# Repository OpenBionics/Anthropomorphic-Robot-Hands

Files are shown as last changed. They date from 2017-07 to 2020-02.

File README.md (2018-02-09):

# OpenBionics - Anthropomorphic Robot Hands

Anthropomorphic, adaptive robot hand with tendon-driven, multidirectional fingers. The fingers employ an actuation mechanism that can achieve both flexion/extension and adduction/abduction concurrently in the metacarpophalangeal (MCP) joint, using two actuators. The two actuators offer increased power transmission during the execution of precise grasping and dexterous, in-hand manipulation tasks. A design optimization framework utilizes results of hand anthropometry studies to derive key parameters of the actuation design.

## Contents

In this repository you can find:
* CAD files of a bidirectional finger 
* ROS package software for dual actuators operation
* Design optimization framework 
* Archive of prototype images
* CAD files of the anthropomorphic robot hand will be uploaded soon

## Notes

Please open a [GitHub issue](https://github.com/OpenBionics/Anthropomorphic-Robot-Hands/issues) if you encounter any problem.

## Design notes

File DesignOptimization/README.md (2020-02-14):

## Introduction

A design optimization framework to derive optimal differential mechanism parameters, according to abduction motion of metacarpophalangeal (MCP) joint. For the index adduction/abduction, we employ the selectively lockable differential mechanism that has the ability to vary its displacement when fingers are locked. To simplify the kinematic analysis, we assume that tendons remain vertical and the input force of the differential mechanism is equally distributed to the remaining 3 digits.

## Working Example

In Figure 1, the design optimization parameters of the differential mechanism are presented.

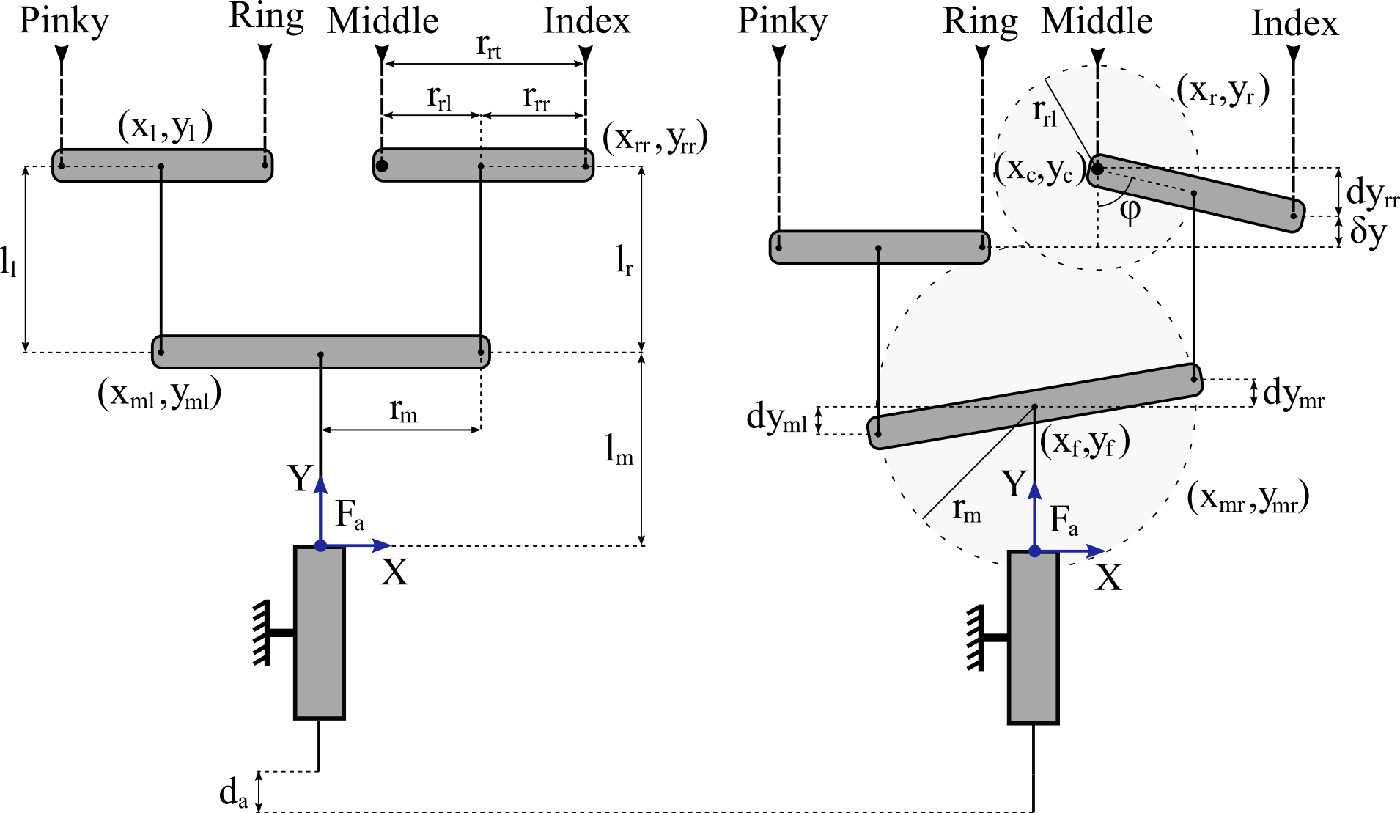
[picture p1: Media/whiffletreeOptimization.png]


Figure 1. Design optimization parameters.

Given the actuator displacement d<sub>a</sub>, the main bar radius r<sub>m</sub>, the index bar radius r<sub>rl</sub>, the length of tendon tendon from actuator to the main bar l<sub>m</sub>, and the length of tendon tendon from the main bar to the index bar l<sub>r</sub>, we obtain the configuration of the index bar (x<sub>r</sub>,y<sub>r</sub>) and of the main bar (x<sub>mr</sub>,y<sub>mr</sub>) by solving a nonlinear equality constraint optimization scheme. Next, we can derive the full configuration of the differential mechanism. 

## Notes

Please open a [GitHub issue](https://github.com/OpenBionics/Anthropomorphic-Robot-Hands/issues) if you encounter any problem.

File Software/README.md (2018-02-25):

## Introduction

The OpenBionics hand_controller ROS package. With this package you 2 [Dynamixel RX-28](http://support.robotis.com/en/product/actuator/dynamixel/rx_series/rx-28.htm) servo motors can be controlled concurrenlty in ROS, along with an [external power supply](http://www.trossenrobotics.com/p/power-supply-12vdc-5a.aspx), a [power supply adapter](http://www.robotis.us/smps2dynamixel/), and a [USB2Dynamixel adapter](http://support.robotis.com/en/product/auxdevice/interface/usb2dxl_manual.htm). Note that there are various ways to implement the control of the 2 Dynamixel, but our suggestion is similar with our tested experimental procedure.

## Installation
This package has been developed and tested in ROS Indigo on Ubuntu 14.04.5 LTS. After ROS installation, create a workspace.

```
$ mkdir -p ~/hand_ws/src
$ cd ~/hand_ws/src
$ catkin_init_workspace
```

Next, clone the hand_controller package and the dependencies in the src directory.
```
$ cd ~/hand_ws/src 
$ git clone https://github.com/OpenBionics/Anthropomorphic-Robot-Hands.git
$ git clone https://github.com/vanadiumlabs/arbotix_ros.git
$ git clone https://github.com/arebgun/dynamixel_motor
```

Then, compile the code and source the workspace.
```
$ cd ~/hand_ws/ 
$ catkin_make
$ . devel/setup.bash
```

Make all the files executable.
```
$ cd ~/hand_ws/src/hand_controller/src/ 
$ chmod +x hand_controller_flex.py && chmod +x hand_controller_adduction.py && chmod +x double_motor_publisher.py && chmod +x double_motor_publisher_sequence.py
```

## Working Example
Connect the servo motors, the USB2Dynamixel, and the power supply as shown [here](http://support.robotis.com/en/product/auxdevice/interface/usb2dxl_manual.htm). Then, check that the USB2Dynamixel adapter is properly connected.
```
$ ls /dev/ttyUSB*
```
If you get ```/dev/ttyUSB0``` continue the procudre, if not check the list bellow.
* If you get  ```/dev/ttyUSB1```, unplug all your USB devices and plug only the USB2Dynamixel adapter. An alternative solution is to navigate to the main controller launch file and change the port name.
```
$ cd ~/hand_ws/src/hand_controller/hand_controller/launch
$ gedit controller_hand_manager.launch
```
Then source the workspace again.
```
$ . devel/setup.bash
```
* If you get permission denied error, change the permissions of the user from the home directory.
```
$ sudo chmod 777 /dev/ttyUSB0
```

In a new terminal run a roscore.
```
$ roscore
```
Set the servo motors IDs through the arbotix_terminal application. 
```
$ arbotix_terminal /dev/ttyUSB0 57142 # The baud rate of Dynamixel AX-12  is 1000000
```
From the arbotix_terminal application list the motors.
```
>> ls
```
To rearrange the IDs, connect only the first servo motor and move its ID.
```
>> mv 1 2
```
Then connect both servo motors and list them.
```
>> ls
```
You should get.
```
   1    2 .... .... .... .... .... .... ....
.... .... .... .... .... .... .... .... ....
```
Exit the arbotix_terminal application (Ctrl-C) and the roscore. Start the controller manager.
```
$ roslaunch hand_controller controller_hand_manager.launch
```
Then, start the controllers for each servo motor.
```
$ roslaunch hand_controller start_flex_controller.launch
$ roslaunch hand_controller start_adduction_controller.launch
```

Next, get feedback from the flexion and the abduction servo motor.
```
$ rosrun hand_controller hand_controller_flex.py
$ rosrun hand_controller hand_controller_adduction.py
```

To control the servo motors.
```
$ rosrun hand_controller double_motor_publisher.py 1.5 1.0 
```
The last numbers represent the servo motor positions for the flexion and the abduction respectively. Note that the desired servo motor positions are absolute and in radians. Since the servo motors can rotate from 0-300<sup>o</sup>, the equivalent radian angles are 0-5.235 rad. In our working example the flexion motor desired position is 57.3<sup>o</sup> and the abduction motor desired position is 85.9<sup>o</sup>.

In case you want to control the motors sequenceally.
```
$ rosrun hand_controller double_motor_publisher_sequence.py
```
You can watch the manipulation of a cylindrical object with this sequence [here](https://youtu.be/w6tnvIsw6BY).

## Notes
Please open a [GitHub issue](https://github.com/OpenBionics/Anthropomorphic-Robot-Hands/issues) if you encounter any problem.

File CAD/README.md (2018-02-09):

## Introduction

The CAD files of a bidirectional finger equipped with a tendon-driven actuation mechanism. The metacarpophalangeal (MCP) joint can implement both flexion/extension and adduction/abduction concurrently, using 2 actuators.

## Contents

In this folder you can find:
* CAD files of a bidirectional finger test bed (SLDPRT) 
* CAD files for 3D printing (STL)
* CAD files of Dynamixel AX-12 as found [here](https://grabcad.com/library/dynamixel-ax-12a-1)

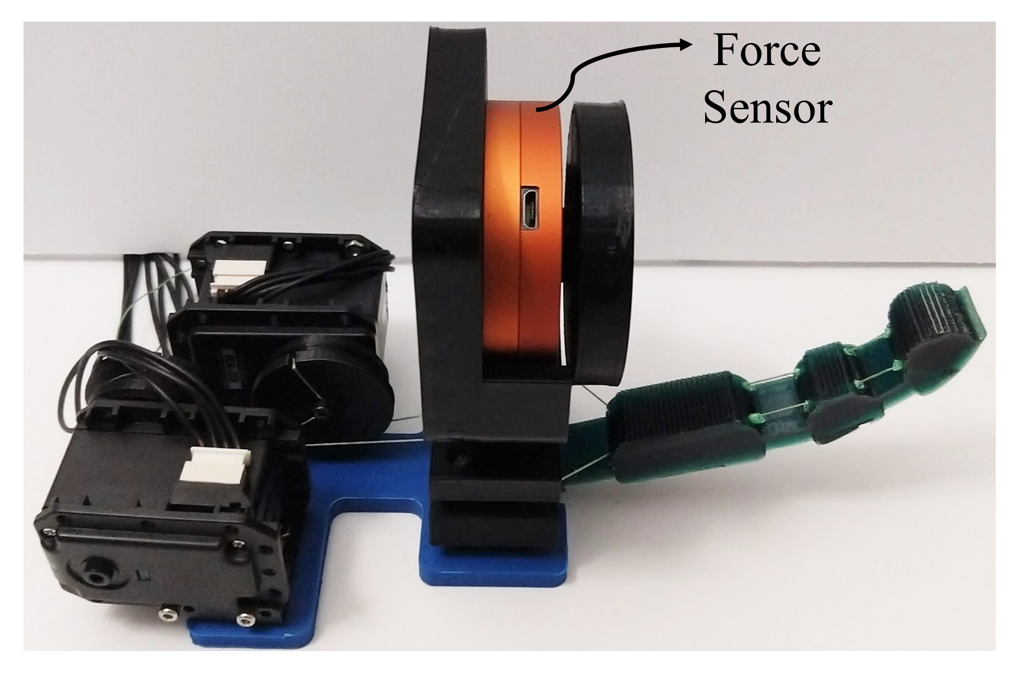
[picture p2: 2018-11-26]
Media/forceSensor.png

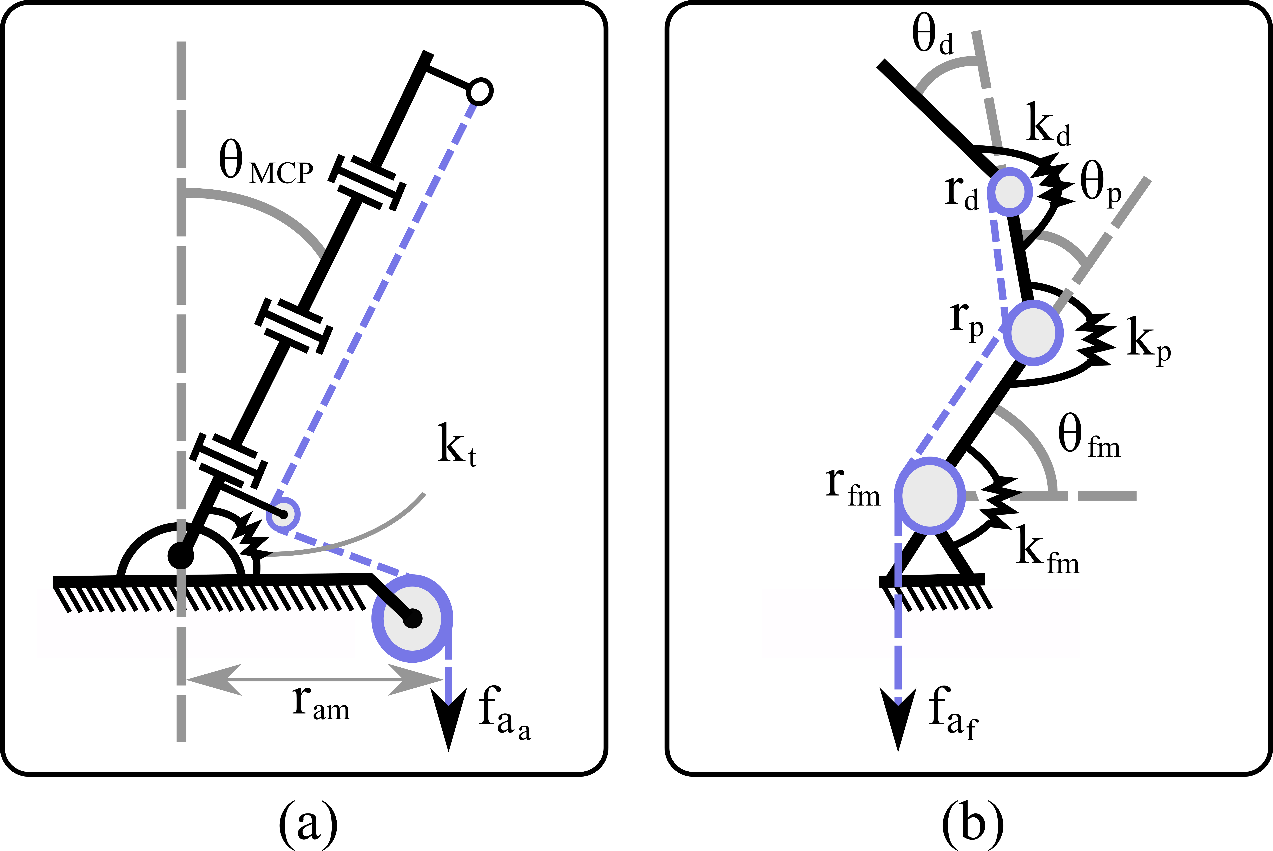
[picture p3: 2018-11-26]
Media/fingerModelAnalysis_col.png

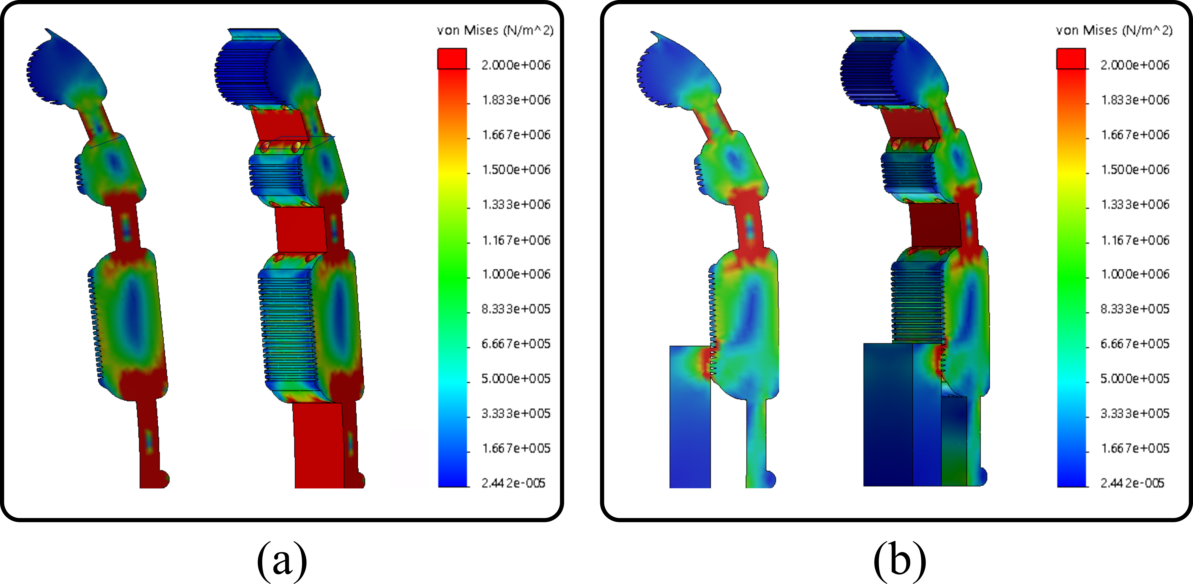
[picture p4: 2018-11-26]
Media/fingerStressAnalysis.png

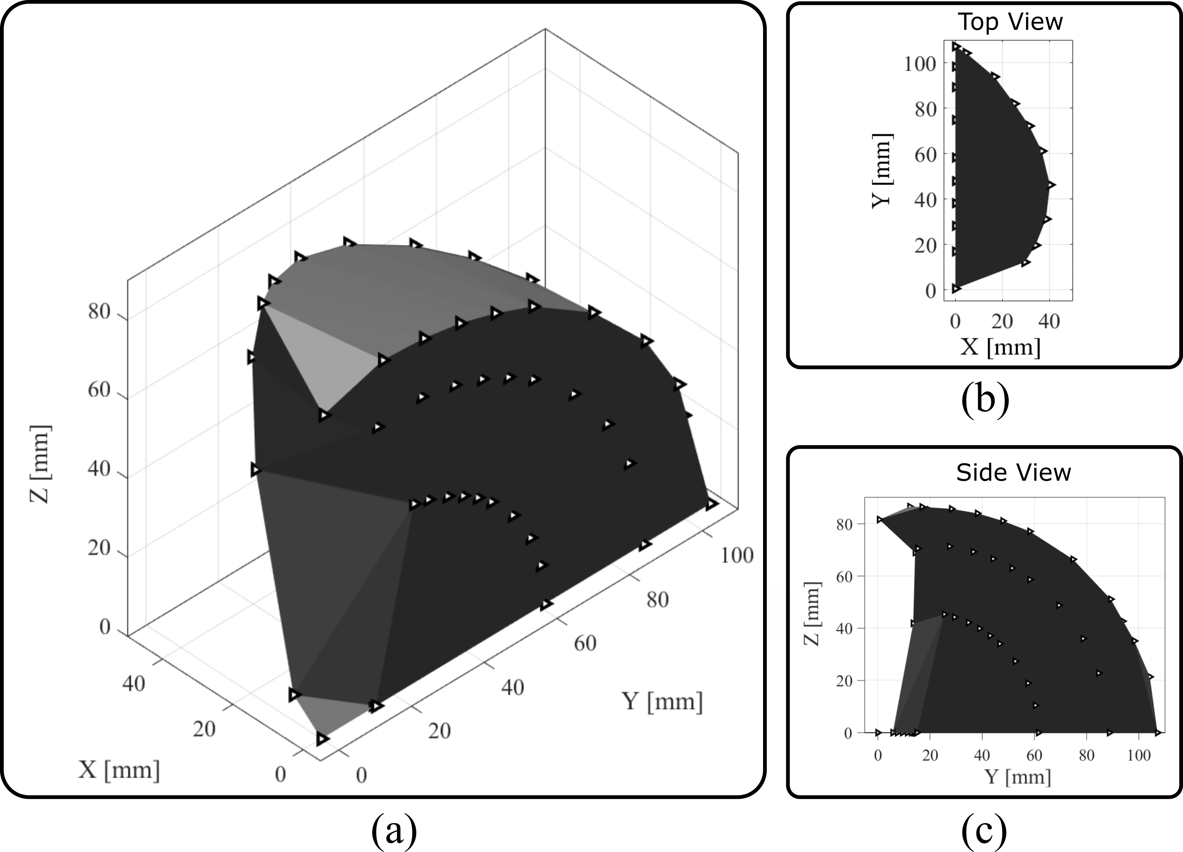
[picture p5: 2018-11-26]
Media/Workspace.png

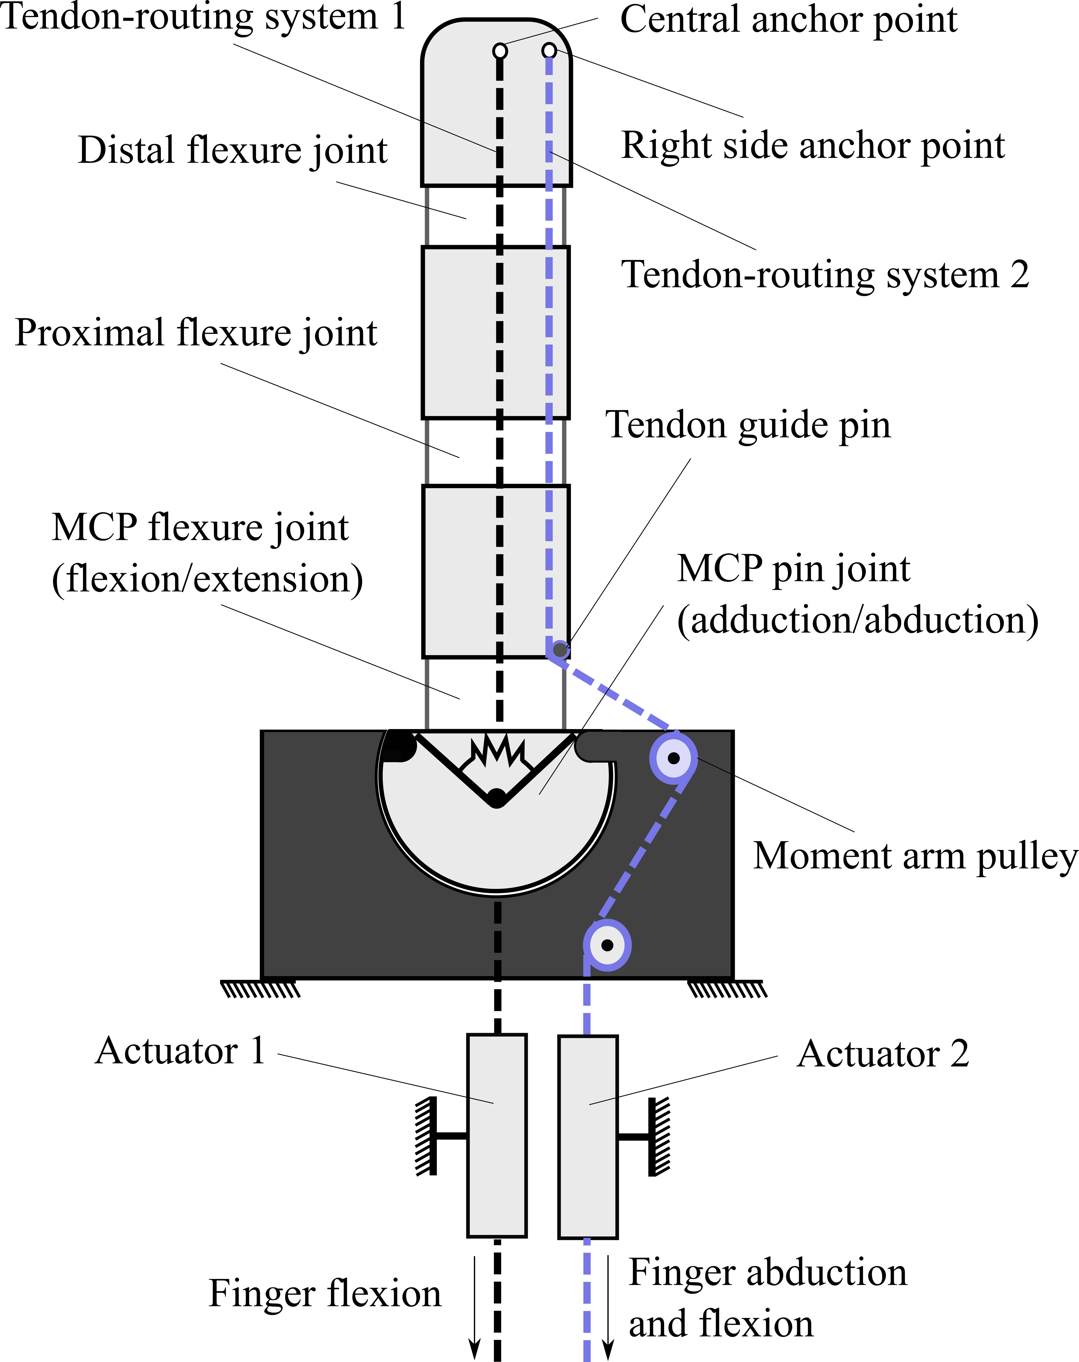
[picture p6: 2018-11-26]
Media/fingerSketch2_1_col.png

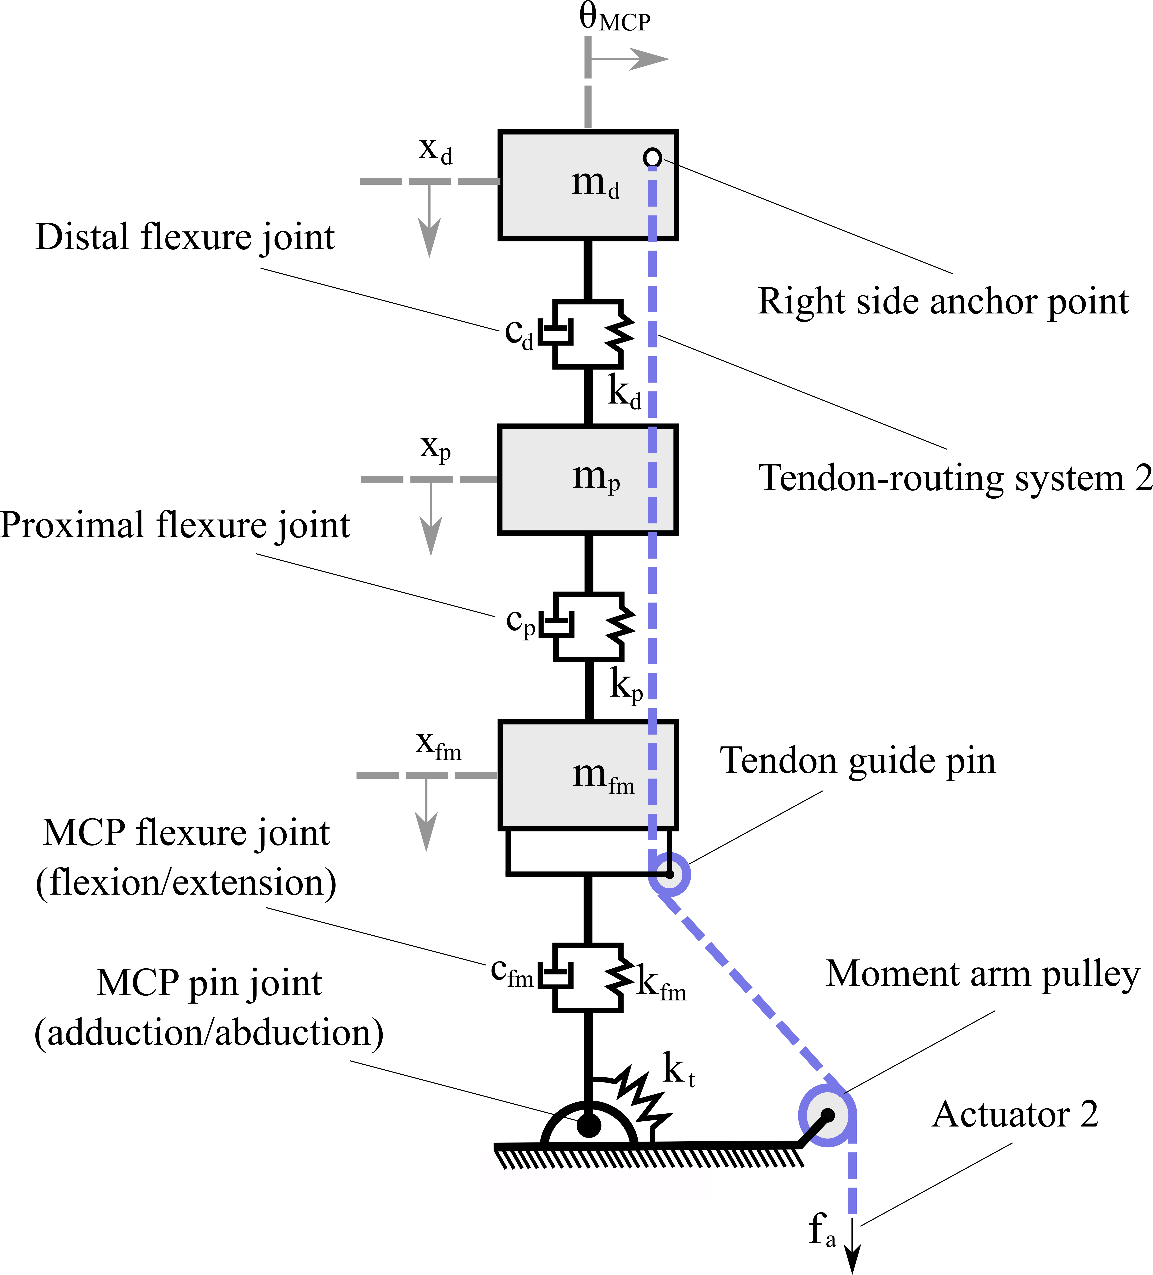
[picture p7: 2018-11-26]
Media/fingerModel_col.png

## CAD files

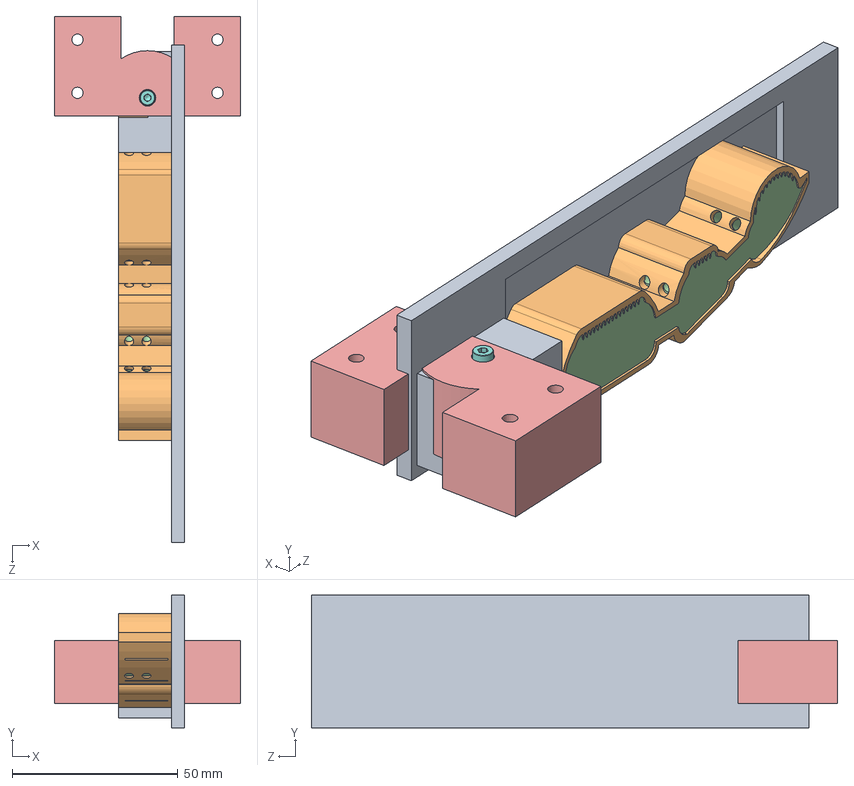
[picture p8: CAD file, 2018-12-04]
CAD/FingersHDM/src/index/indexMoldAssembly.SLDASM
56.2 x 40.0 x 158.5 mm
rotatingFingerLink
indexHDM
base
coilSpring
hex thin nut chamfered gradeab_iso
socket head cap screw_iso

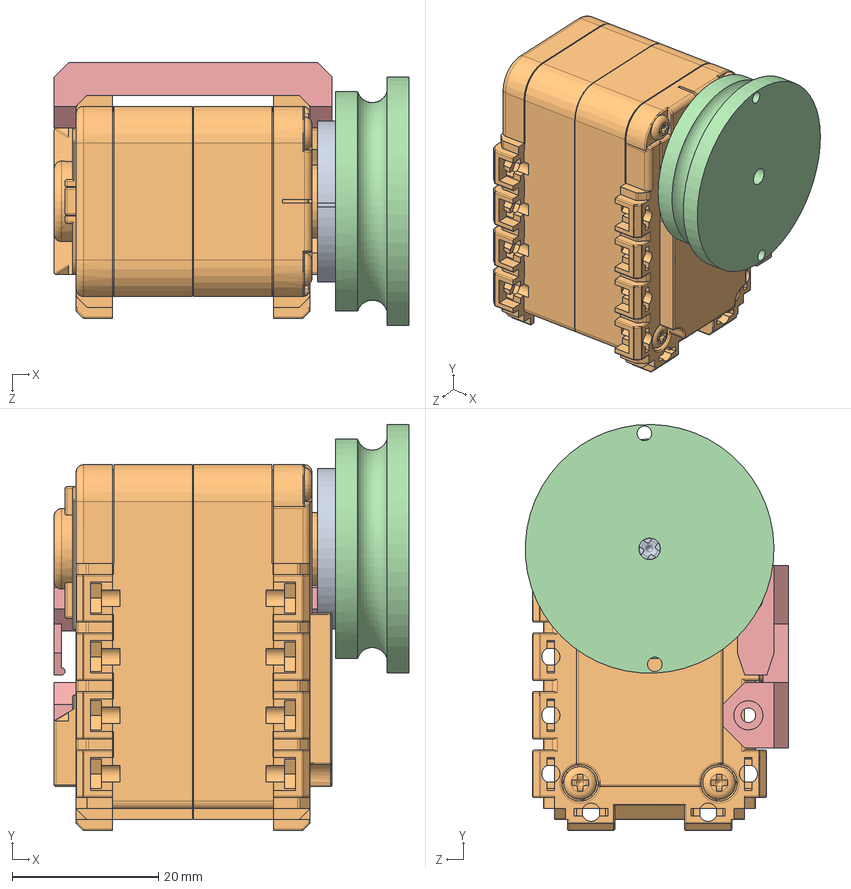
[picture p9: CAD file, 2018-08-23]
CAD/Servo/AX12_Base.SLDASM
48.5 x 55.5 x 36.0 mm
ax12_wheel
ax12_box
ax12_cog
servoPulleyRX28
AX12Base

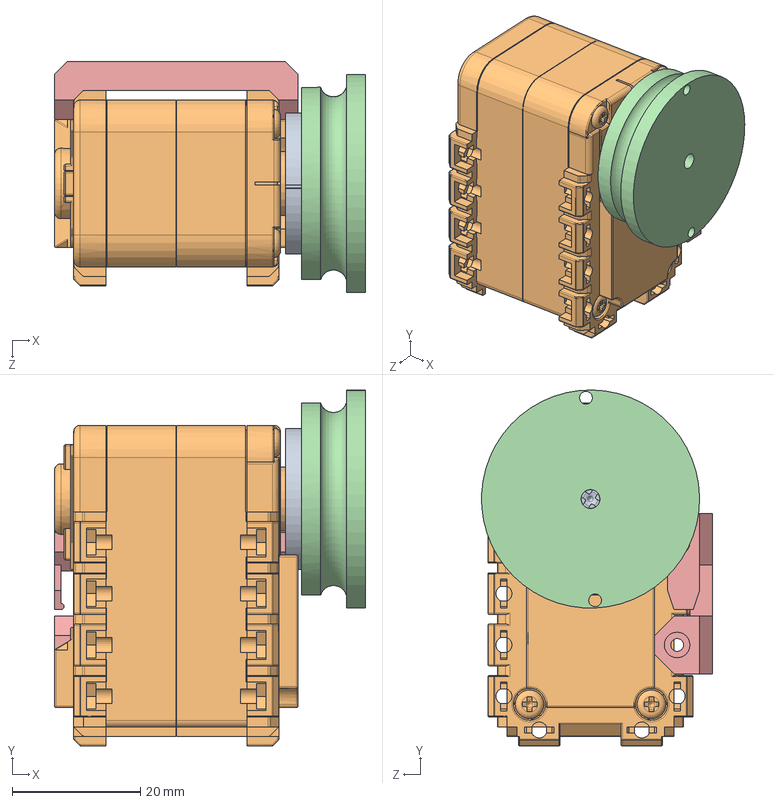
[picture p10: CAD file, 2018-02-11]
CAD/Servo/AX12_BaseR.SLDASM
48.5 x 55.5 x 36.0 mm
ax12_wheel
ax12_box
ax12_cog
servoPulleyRX28
AX12Base

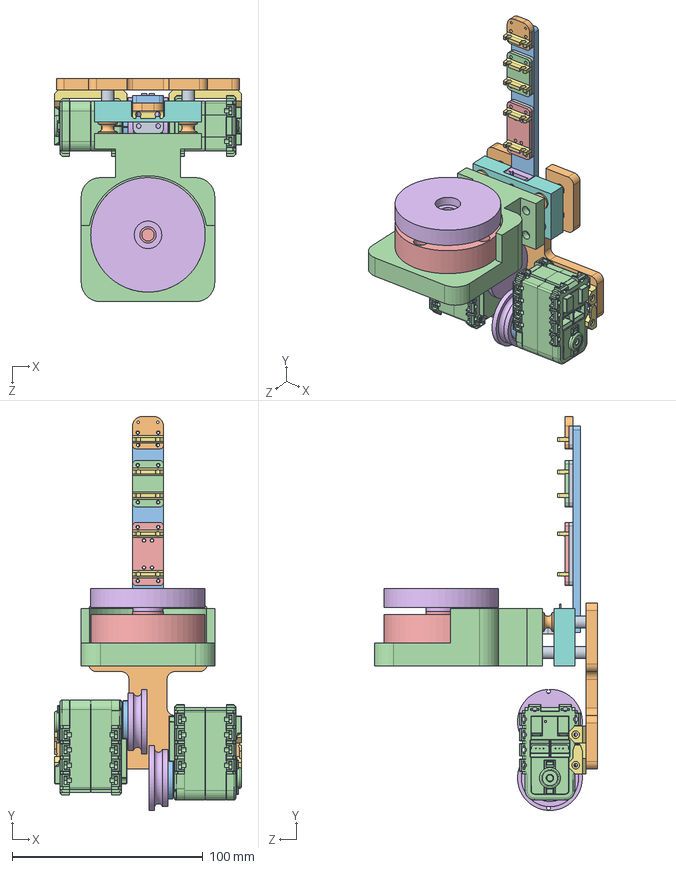
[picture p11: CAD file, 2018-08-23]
CAD/BidirectionalFinger/BidirectionalFinger.SLDASM
98.0 x 206.4 x 117.0 mm
middleJointBase
middleDIP
middleElastomer
middleMIP
middlePIP
rotatingFingerBase
tubeDriver x 5
palmUpBase
thumbMechanismDriver
base
ax12_wheel x 2
ax12_box x 2
ax12_cog x 2
servoPulleyRX28 x 2
AX12Base x 2
hexalobular socket pan head_iso x 5
spacer x 6
spacePulley x 2
coilSpring
forceSensorBase
VarienseFS101
forceSurface

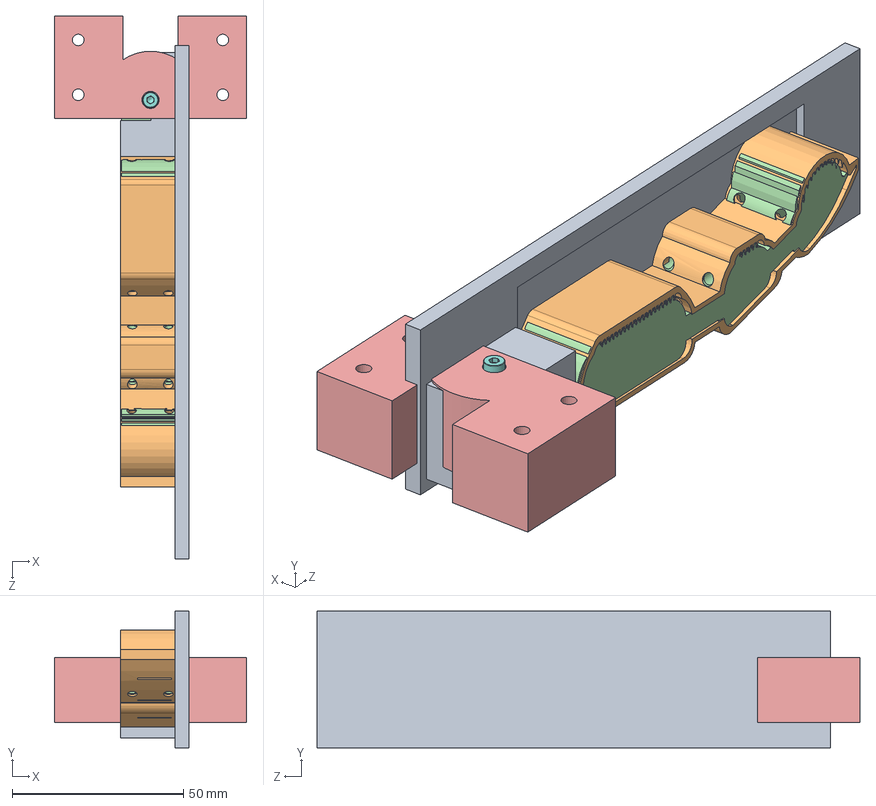
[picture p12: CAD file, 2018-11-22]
CAD/FingersHDM/src/thumb/fingerMoldAssembly.SLDASM
56.2 x 40.0 x 158.5 mm
rotatingFingerLink
fingerHDM
base
coilSpring
hex thin nut chamfered gradeab_iso
socket head cap screw_iso

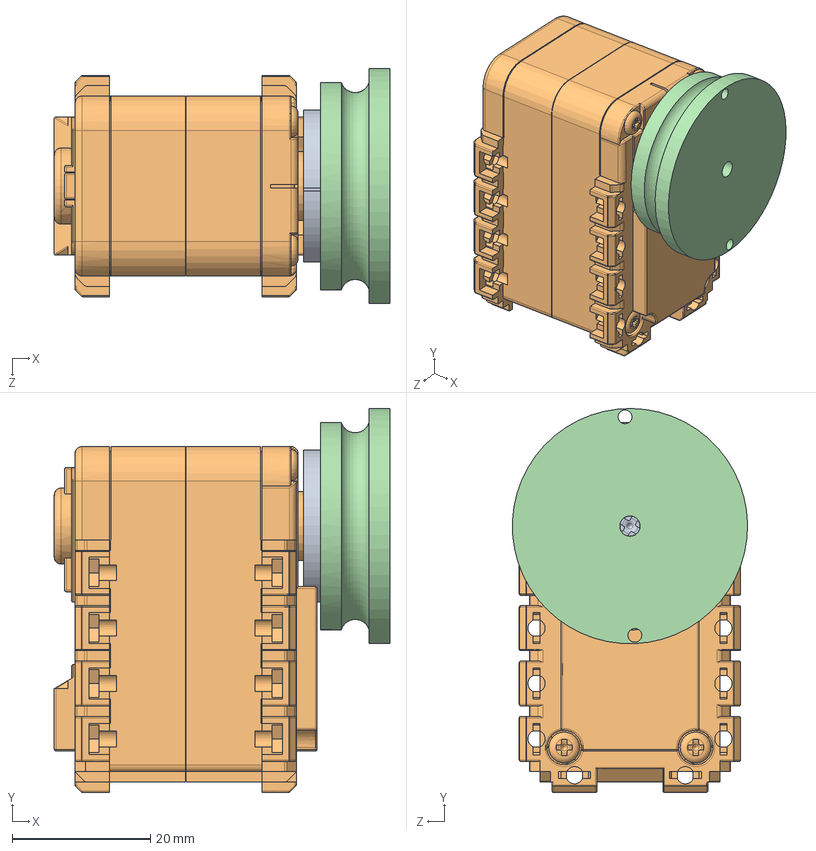
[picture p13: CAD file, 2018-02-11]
CAD/Servo/AX12.SLDASM
48.5 x 55.5 x 34.0 mm
ax12_wheel
ax12_box
ax12_cog
servoPulleyRX28

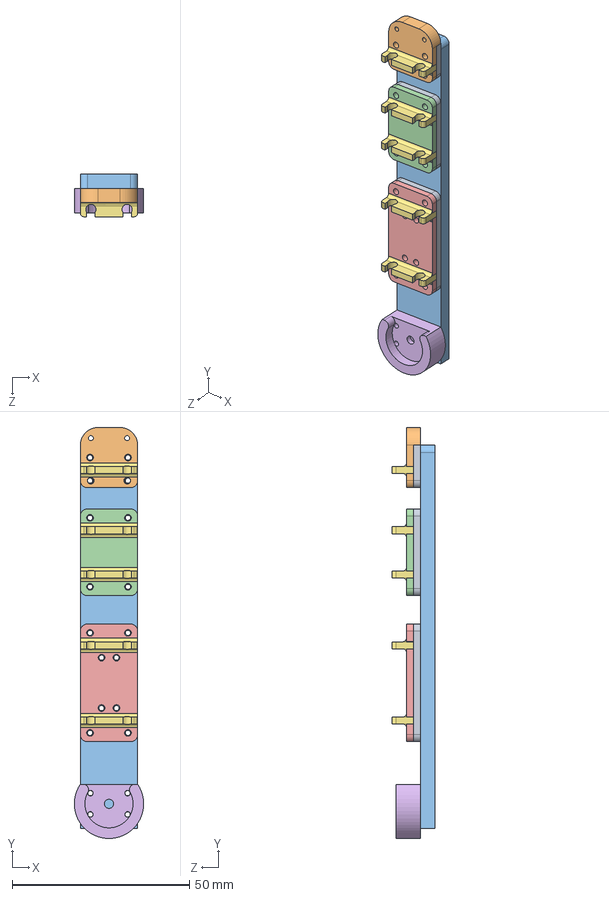
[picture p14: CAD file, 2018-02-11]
CAD/BidirectionalFinger/Middle.SLDASM
19.6 x 115.9 x 12.0 mm
middleJointBase
middleDIP
middleElastomer
middleMIP
middlePIP
rotatingFingerBase
tubeDriver x 5

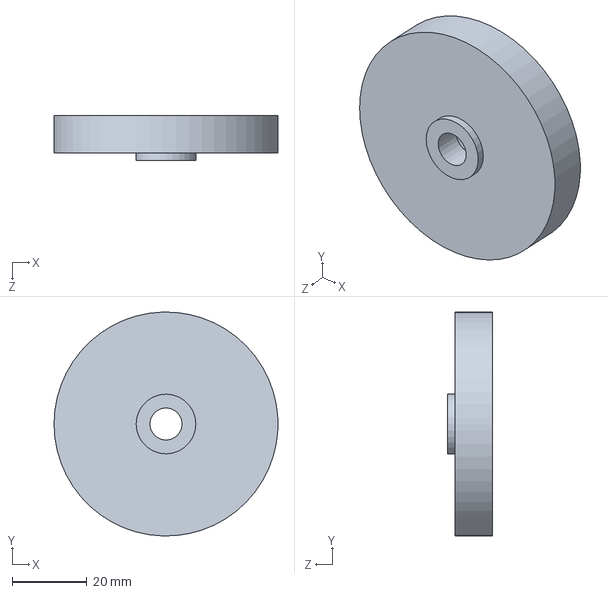
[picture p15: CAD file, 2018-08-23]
CAD/BidirectionalFinger/forceSurface.SLDPRT
60.0 x 60.0 x 12.0 mm

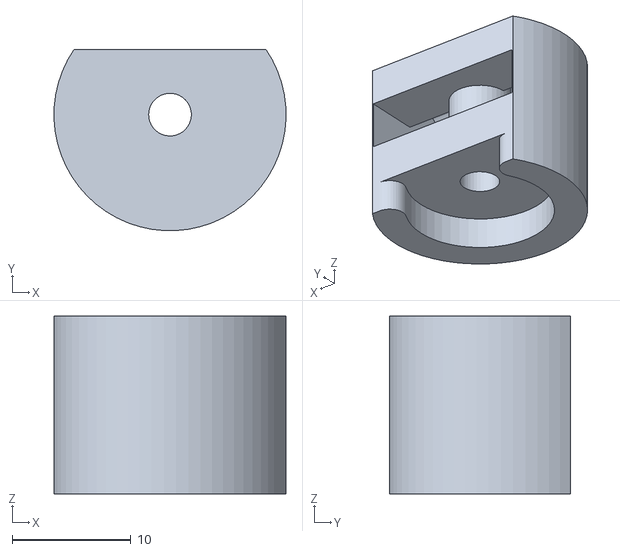
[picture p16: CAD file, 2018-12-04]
CAD/FingersHDM/commonParts/rotatingFingerLink.STL
19.6 x 15.3 x 15.0

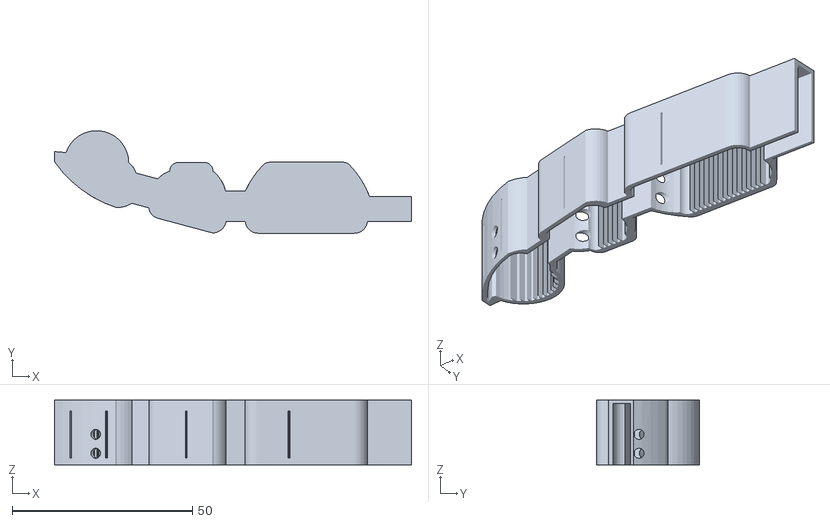
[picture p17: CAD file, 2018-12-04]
CAD/FingersHDM/index/indexMold.STL
98.9 x 28.4 x 18.0

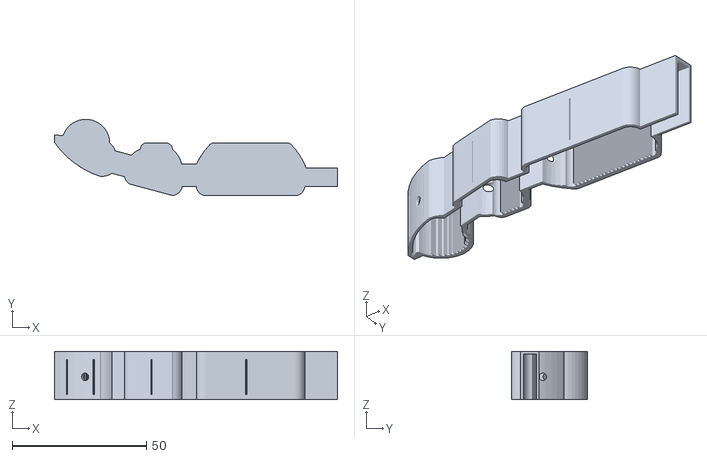
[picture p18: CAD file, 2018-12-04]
CAD/FingersHDM/middle/middleMold.STL
105.4 x 28.4 x 18.0

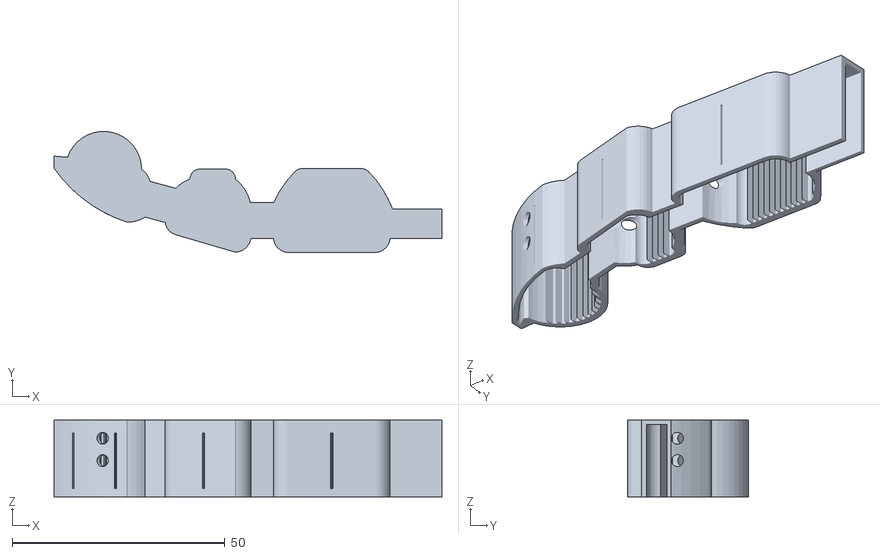
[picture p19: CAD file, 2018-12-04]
CAD/FingersHDM/pinky/pinkyMold.STL
91.1 x 28.4 x 18.0

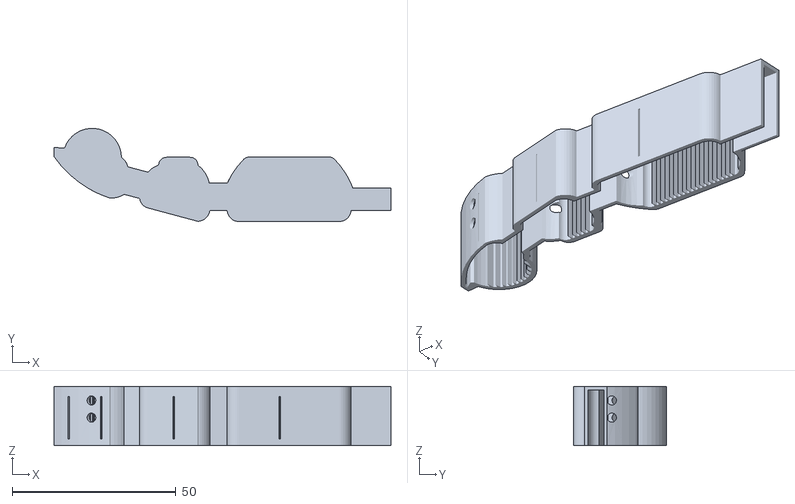
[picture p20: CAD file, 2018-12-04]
CAD/FingersHDM/ring/ringMold.STL
102.8 x 28.4 x 18.0

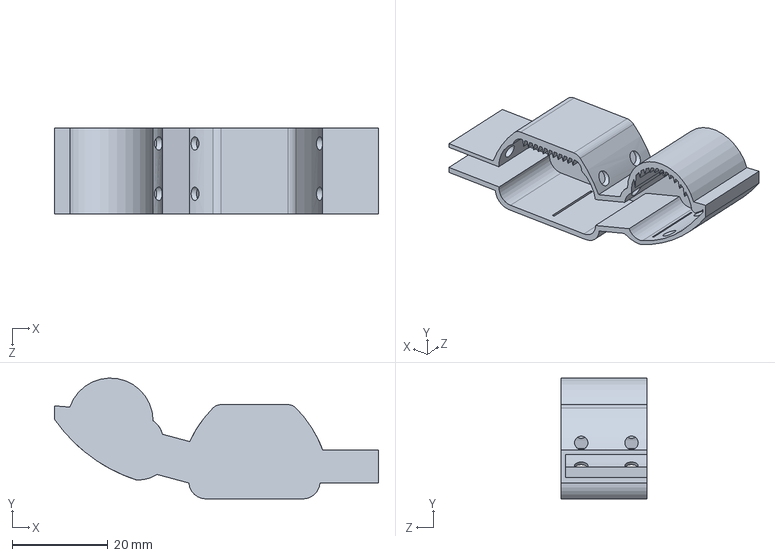
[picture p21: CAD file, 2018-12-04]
CAD/FingersHDM/src/thumb/thumbMold.SLDPRT
67.6 x 25.2 x 18.0 mm

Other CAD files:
CAD/FingersHDM/src/commonParts/rotatingFingerLink.SLDPRT
CAD/FingersHDM/src/middle/middleMold.SLDPRT
CAD/FingersHDM/src/pinky/pinkyMold.SLDPRT
CAD/FingersHDM/src/ring/ringMold.SLDPRT
CAD/BidirectionalFinger/CylindricalObject.SLDPRT
CAD/BidirectionalFinger/VarienseFS101.SLDPRT
CAD/BidirectionalFinger/base.SLDPRT
CAD/BidirectionalFinger/coilSpring.SLDPRT
CAD/BidirectionalFinger/forceSensorBase.SLDPRT
CAD/BidirectionalFinger/middleDIP.SLDPRT
CAD/BidirectionalFinger/middleElastomer.SLDPRT
CAD/BidirectionalFinger/middleJointBase.SLDPRT
CAD/BidirectionalFinger/middleMIP.SLDPRT
CAD/BidirectionalFinger/middlePIP.SLDPRT
CAD/BidirectionalFinger/palmUpBase.SLDPRT
CAD/BidirectionalFinger/rotatingFingerBase.SLDPRT
CAD/BidirectionalFinger/servoPulleyRX28.SLDPRT
CAD/BidirectionalFinger/spacePulley.SLDPRT
CAD/BidirectionalFinger/spacer.SLDPRT
CAD/BidirectionalFinger/stabeFinger.SLDPRT
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

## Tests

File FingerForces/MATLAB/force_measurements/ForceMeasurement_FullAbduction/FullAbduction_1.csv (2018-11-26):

Timestamp | Force Z | Comments
0 | -0.77
6 | -2.42
11 | -0.39
17 | -0.79
23 | -1.08
29 | -0.85
34 | 0.04
40 | -0.37
46 | -0.02
52 | -1.47
57 | -0.48
63 | -0.66
69 | -2.28
74 | -0.95
80 | -1.41
86 | -1.53
92 | -1.22
97 | -1.51
103 | -1.86
109 | -1.51
115 | -1.92
120 | -0.25
126 | -0.71
132 | -0.43
137 | -1.12
143 | -1.06
149 | -0.33
155 | -1.49
160 | -0.97
166 | -0.91
172 | 0.08
178 | -1.03
183 | -0.56
189 | -1.55
195 | -0.74
200 | -0.39
206 | -1.51
212 | -0.70
218 | -0.99
223 | -1.63
229 | -1.05
235 | -1.76
241 | -0.95
246 | -0.77
252 | -0.77
258 | -0.77
263 | -0.08
269 | -0.54
275 | -0.19
281 | 0.10
286 | 0.50
292 | -0.54
298 | -0.54
304 | 0.27
309 | 0.04
315 | 0.04
321 | -0.39
326 | -1.26
332 | -0.91
338 | -0.62
344 | -0.56
349 | -0.54
355 | -0.95
361 | -0.77
367 | -1.24
372 | -0.37
378 | -1.04
384 | -0.81
389 | 0.52
395 | -0.64
401 | -0.58
407 | -0.95
412 | -1.29
418 | -1.18
424 | -2.63
429 | -1.06
435 | -0.53
441 | -1.16
447 | -0.93
452 | -0.70
458 | -1.05
464 | -1.37
470 | -0.62
475 | -0.68
481 | -0.68
487 | -2.24
492 | -0.43
498 | -0.95
504 | -0.83
510 | -1.58
515 | -0.66
521 | -0.79
527 | -0.45
533 | -0.50
538 | -0.21
544 | -0.39
550 | -2.73
555 | -0.64
561 | -0.53
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

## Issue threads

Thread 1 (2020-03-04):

πτυχιακη

staurosr, 2020-03-04:
Γεια σας, κύριε Γκοντούδη , θα κάνω πτυχιακή  ένα ανθρωπομορφικό χέρι, είμαι κυριολεκτικά στο 0 ,εσείς απο που θα μου προτείνατε να αρχίσω;;;;;

staurosr, 2020-03-08:
> Γεια σας, κύριε Γκοντούδη , θα κάνω πτυχιακή ένα ανθρωπομορφικό χέρι, είμαι κυριολεκτικά στο 0 ,εσείς απο που θα μου προτείνατε να αρχίσω;;;;;

Closed 2020-03-08.

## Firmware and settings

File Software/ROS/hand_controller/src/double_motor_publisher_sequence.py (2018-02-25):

#!/usr/bin/env python
from std_msgs.msg import Float64
import rospy
import sys

class double_motor_publisher_sequence:
        def __init__(self, mot1, mot2):
            mot1 = float(mot1)
            mot2 = float(mot2)
            self.motor1_pub = rospy.Publisher('/flex_controller/command', Float64, queue_size=1)
            self.motor2_pub = rospy.Publisher('/adduction_controller/command', Float64, queue_size=1)
            ct = 0
            while ct < 5:
                self.motor1_pub.publish(mot1)
                self.motor2_pub.publish(mot2)
                rospy.sleep(.1)
                ct = ct+1

                        
if __name__ == '__main__':
      rospy.init_node('joint_position_tester')
	  double_motor_publisher_sequence(3, 0)
      rospy.sleep(2.0)
      double_motor_publisher_sequence(2.5, 0.3)
      rospy.sleep(3.0)
      double_motor_publisher_sequence(1.2, 1.6)
      rospy.sleep(3)
      double_motor_publisher_sequence(0.9, 1.3)
      rospy.sleep(3)
      double_motor_publisher_sequence(1.5, 1.9)
      rospy.sleep(3)
      double_motor_publisher_sequence(.7, 1.1)
      rospy.sleep(3)
      double_motor_publisher_sequence(1.7, 2.1)
      rospy.sleep(5)
      double_motor_publisher_sequence(.7, 1.1)
      rospy.sleep(5)
      double_motor_publisher_sequence(1.2, 1.6)
      rospy.sleep(5)
      double_motor_publisher_sequence(3, 0)
      rospy.sleep(2.0)

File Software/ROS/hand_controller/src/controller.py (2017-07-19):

#!/usr/bin/env python
# license removed for brevity
import rospy
from std_msgs.msg import String
from std_msgs.msg import Float64

def talker():
    pub = rospy.Publisher('/tilt_controller/command', Float64, queue_size=10)
    rospy.init_node('talker', anonymous=True)
    rate = rospy.Rate(0.2) # 10hz
    while not rospy.is_shutdown():
        hello_str = "hello world %s" % rospy.get_time()
        rospy.loginfo("Close Hand")
        pub.publish(2.4)
        rate.sleep()
	rospy.loginfo("Open Hand")
        pub.publish(.8)
	rate.sleep()

if __name__ == '__main__':
    try:
        talker()
    except rospy.ROSInterruptException:
        pass

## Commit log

2017-07-19 Add CAD files
    [AX12.SLDASM, AX12Base.SLDPRT, AX12_Base.SLDASM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]
2017-07-19 Add design optimization framewrok
2018-02-09 Update CAD model with bidirectional finger
    [AX12.SLDASM, AX12Base.SLDPRT, AX12_Base.SLDASM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]
2018-02-09 Update STL with bidirectianl middle
    [base.STL, middle.STL, palmUpBase.STL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]
2018-02-09 Update servo pulley CAD files
    [AX12.SLDASM, AX12_Base.SLDASM, AX12_BaseR.SLDASM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]
2018-02-11 Update CAD for bidirectional abduction
    [AX12.SLDASM, AX12Base.SLDPRT, AX12_Base.SLDASM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]
2018-02-25 Add cylindrical object for manipulation
    [CylindricalObject.SLDPRT, CylindricalObject.STL]
2018-02-25 Add double motor control in a sequence
2018-08-23 Update right servo and bidirectional finger
    [AX12_Base.SLDASM, BidirectionalFinger.SLDASM]
2018-08-23 Add force sensor setup
    [VarienseFS101.SLDPRT, forceSensorBase.SLDPRT, forceSensorBase.STL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]
2018-11-22 Update finger CAD files
    [base.SLDPRT, coilSpring.SLDPRT, fingerBase.SLDPRT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]
2018-11-26 Add force measurements and analysis
    [FullAbduction_1.csv]
2018-12-04 Update monolithic thumb
    [rotatingFingerLink.SLDPRT, rotatingFingerLink.STL, thumbMold.STL]
2018-12-04 Add monolithic fingers
    [base.SLDPRT, coilSpring.SLDPRT, fingerMold.STL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]
